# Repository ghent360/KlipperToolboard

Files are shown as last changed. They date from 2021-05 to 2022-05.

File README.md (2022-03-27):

# Huvud 3D Printer toolhead board
This is a modified version of the KilipperBoard started by bondus(https://github.com/bondus/KlipperToolboard). The goal is to make the board as cheap as possible. Removed the CAN interface, switched to RP4020 MCU since it is more available. Added extra IO pins for LEDs or other sensors.
# Original author words
A very small 3D printer board for use on a direct drive toolhead. It is designed to be used with Klipper firmware. Klipper has the awesome feature to be able to use multiple MCUs connected to the host over a (relatively) high latency connection.

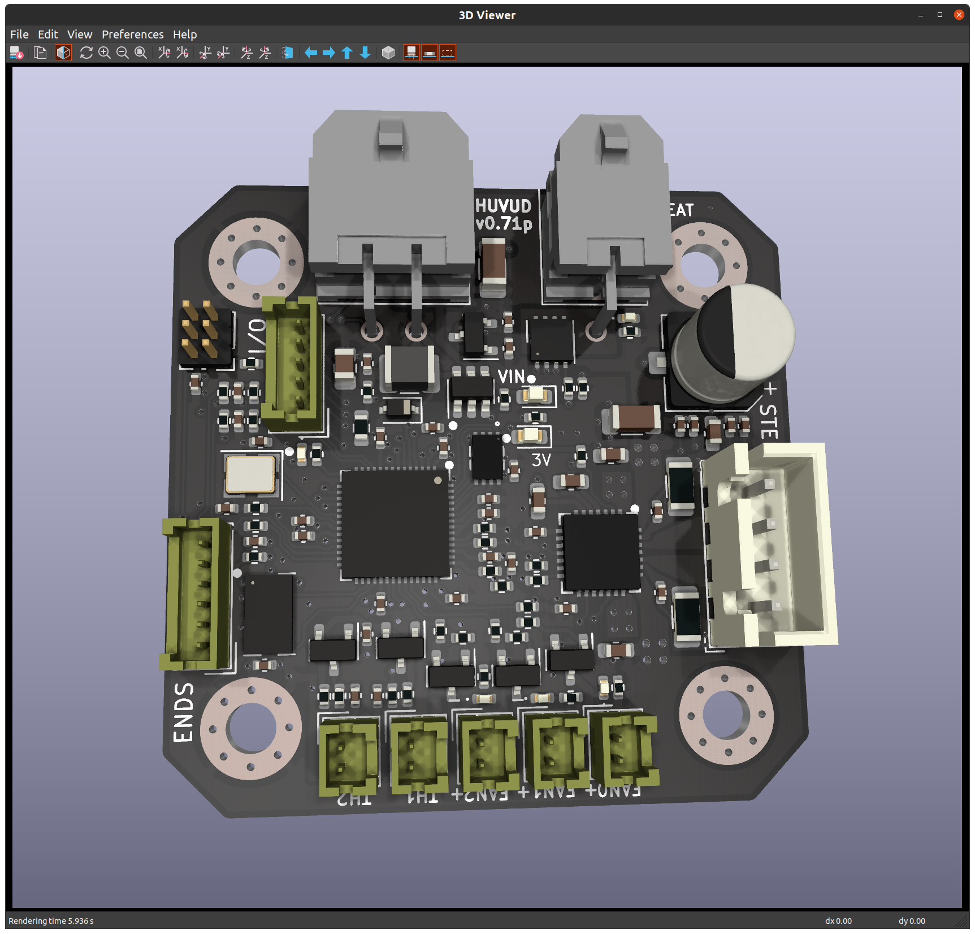
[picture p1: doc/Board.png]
Image of Board


Features: 
* One TMC2209 stepper driver for the extruder
* Three MOSFETs for fans
* One big MOSFET for the hotend heater
* Two thermistor inputs
* ADXL345 accelerometer for resonance testing
* Support for 3 endstops
* 3 extra I/O pins for RGB LEDs or other functions
* RP4020 Dual core 133MHz 32bit ARM MCU
* USB, for flashing firmware

Main power is 12-24V. 24V is preferred to keep the currents low

All done in KiCad and open source. 

If you are interesting in helping out, testing or eventually using this board feel free to contact me at ghent360@iqury.us.

### Documentation

* [Pinout and hook up](doc/pinout.md)
* [Klipper configuration](doc/klipper.md)
* [Prototype versions of the board](doc/versions.md)

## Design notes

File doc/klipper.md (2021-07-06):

## Klipper configuration

### Firmware configuration

* Enable Micro-controller Architecture (STMicroelectronics STM32)
* Pick STM32F103
* Pick Bootloader offset (2KiB bootloader (HID Bootloader))
* Disable Use USB for communication (instead of serial)
* Enable Use CAN for communication (instead of serial)
* Pick CAN pins (Pins PB8(rx) and PB9(tx))

It is possible to use USB instead of the CAN bus, like most other controller boards. 

### Bootloader and Flashing

The boards come preloaded with the HID bootloader for flashing over USB. Note that the board can not be powered over USB. 

To enter the bootloader pin BOOT1 must be connected to 3.3V when the board is powered up or reset. When in the bootloader the green LED will flash quickly. Flash with the command "make flash FLASH_DEVICE=1209:beba"

Hopefully a CAN capable bootloader will be developed to allow flashing over CAN bus.

### printer.cfg

[Example partial printer.cfg](printer.cfg)

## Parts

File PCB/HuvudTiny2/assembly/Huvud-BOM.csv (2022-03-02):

Comment | Designator | Footprint | LCSC | LCSC
0.1uF | C1,C2,C9,C10,C11,C19,C24,C25,C30,C31,C35,C37,C38,C39,C40,C41,C42,C43 | Capacitor_SMD:C_0402_1005Metric |  | C307331
30pF | C12,C13 | Capacitor_SMD:C_0402_1005Metric |  | C1570
10uF/35V | C14,C22 | Capacitor_SMD:C_1206_3216Metric |  | C13585
22uF | C15 | Capacitor_SMD:C_0805_2012Metric |  | C45783
2.2uF | C18,C32,C44 | Capacitor_SMD:C_0402_1005Metric |  | C12530
1nF 50V | C20,C21,C26,C28 | Capacitor_SMD:C_0402_1005Metric |  | C1523
100nF | C29,C36 | Capacitor_SMD:C_0402_1005Metric |  | C1525
0.1uF/35V | C3,C6,C7,C16 | Capacitor_SMD:C_0603_1608Metric |  | C14663
4.7uF | C4,C17,C33,C34 | Capacitor_SMD:C_0402_1005Metric |  | C23733
22nf/50V | C5 | Capacitor_SMD:C_0603_1608Metric |  | C21122
100uF/35V | C8 | Capacitor_SMD:CP_Elec_6.3x7.7 |  | C134792
LEDGR | D1,D2,D3,D5,D10 | LED_SMD:LED_0402_1005Metric |  | C130723
1N5819WS | D4 | Diode_SMD:D_SOD-323 |  | C191023
LEDRED | D6,D8 | LED_SMD:LED_0603_1608Metric |  | C2286
BAT54S | D7,D9 | Package_TO_SOT_SMD:SOT-23 |  | C12765
MountingHole | H1,H2,H3,H4 | MountingHole:MountingHole_3.2mm_M3_Pad_Via
MOLEX Micro Fit 2x2 | J1 | Connector_Molex:Molex_Micro-Fit_3.0_43045-0400_2x02_P3.00mm_Horizontal |  | C122413
FAN0 | J10 | Connector_Hirose:Hirose_DF13-02P-1.25DSA_1x02_P1.25mm_Vertical |  | C10819
IO | J11 | Connector_Hirose:Hirose_DF13-05P-1.25DSA_1x05_P1.25mm_Vertical |  | C220124
DBG | J2 | Connector_PinHeader_1.27mm:PinHeader_2x03_P1.27mm_Vertical
THERM | J3,J8 | Connector_Hirose:Hirose_DF13-02P-1.25DSA_1x02_P1.25mm_Vertical |  | C10819
FAN1 | J4 | Connector_Hirose:Hirose_DF13-02P-1.25DSA_1x02_P1.25mm_Vertical |  | C10819
FAN2 | J5 | Connector_Hirose:Hirose_DF13-02P-1.25DSA_1x02_P1.25mm_Vertical |  | C10819
Heater | J6 | Connector_Molex:Molex_Micro-Fit_3.0_43045-0200_2x01_P3.00mm_Horizontal |  | C122431
Endstop | J7 | Connector_Hirose:Hirose_DF13-06P-1.25DSA_1x06_P1.25mm_Vertical |  | C10823
STEPPER | J9 | Connector_JST:JST_XH_B4B-XH-A_1x04_P2.50mm_Vertical |  | C492489
6.8uH | L1 | Inductor_SMD:L_1210_3225Metric |  | C223222
Logo_Open_Hardware_Small | LOGO1 | Symbol:OSHW-Symbol_6.7x6mm_SilkScreen
Net-Tie_2 | NT1 | NetTie:NetTie-2_SMD_Pad0.5mm
AO3400A | Q1,Q2,Q4 | Package_TO_SOT_SMD:SOT-23 |  | C20917
AON7534 | Q3 | Huvud:DFN-8-1EP_3x3mm_P0.65mm_EP1.7x2.05mm |  | C341712
4.7k | R2,R9 | Resistor_SMD:R_0402_1005Metric |  | C25900
13k | R21 | Resistor_SMD:R_0603_1608Metric |  | C22797
68k | R22 | Resistor_SMD:R_0402_1005Metric |  | C36871
1 | R25 | Resistor_SMD:R_0402_1005Metric |  | C25086
200 | R26 | Resistor_SMD:R_0402_1005Metric |  | C25087
22 | R27,R28,R34,R35 | Resistor_SMD:R_0402_1005Metric |  | C25092
1k | R3,R6,R16,R20,R30 | Resistor_SMD:R_0402_1005Metric |  | C11702
27.4 | R31,R37 | Resistor_SMD:R_0402_1005Metric |  | C31439
0.1 1% | R4,R7 | Resistor_SMD:R_1206_3216Metric |  | C25334
10k | R5,R8,R10,R12,R13,R14,R15,R17,R18,R19,R23,R24,R29,R32,R33,R36,R38,R42,R43 | Resistor_SMD:R_0402_1005Metric |  | C25744
ADXL345 | U1 | Package_LGA:LGA-14_3x5mm_P0.8mm_LayoutBorder1x6y |  | C9667
TMC2209-LA | U2 | Huvud:TMC22xx_QFN |  | C465949
RP2040 | U3 | RP2040_minimal:RP2040-QFN-56 |  | C2040
EUP3458 | U4 | Package_TO_SOT_SMD:SOT-23-6 |  | C89300
XC6206PxxxMR | U5 | Package_TO_SOT_SMD:SOT-23 |  | C5446
W25Q16JVUXIQ | U6 | W25Q16JVUXIQ |  | C2843335
12MHz | Y1 | Crystal:Crystal_SMD_3225-4Pin_3.2x2.5mm |  | C9002

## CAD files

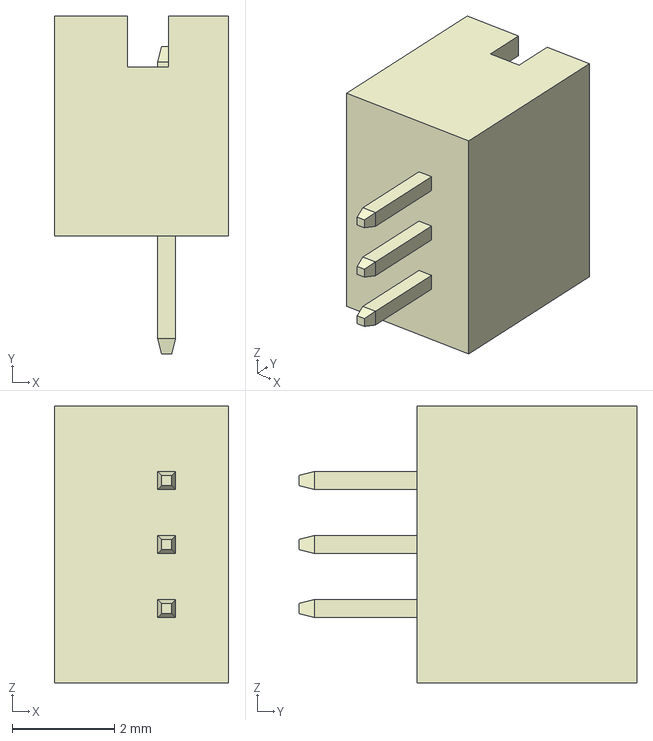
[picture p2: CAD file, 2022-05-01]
PCB/HuvudTiny2/3D/DF13-3P-1.25DSA.stp
3.40 x 6.60 x 5.40 mm

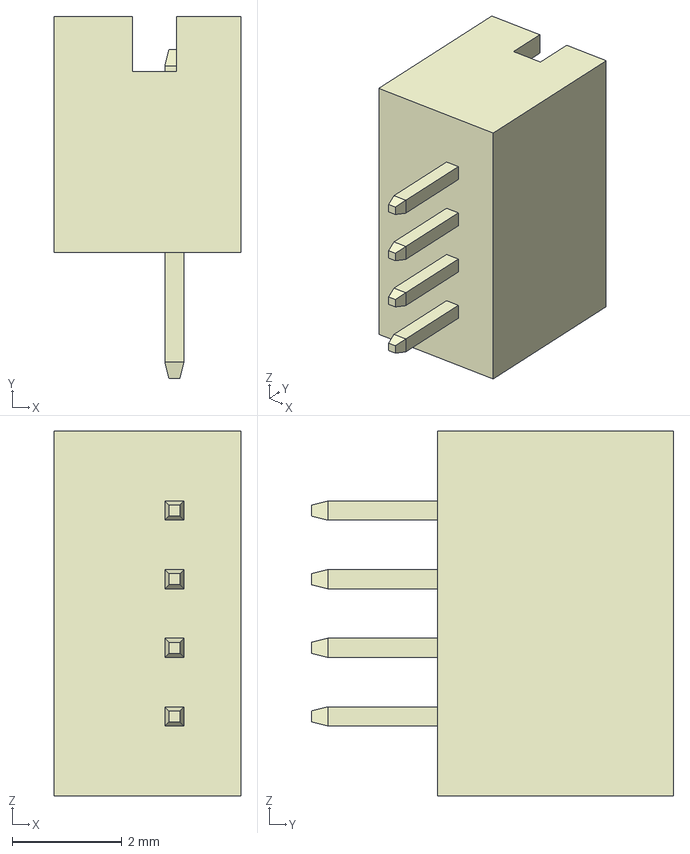
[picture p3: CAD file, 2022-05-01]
PCB/HuvudTiny2/3D/DF13-4P-1.25DSA.stp
3.40 x 6.60 x 6.65 mm

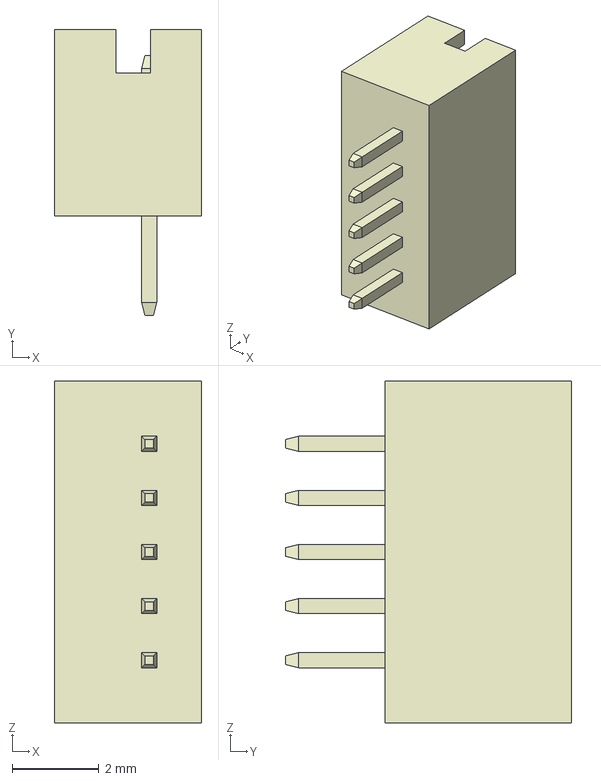
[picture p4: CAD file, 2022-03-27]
PCB/HuvudTiny2/3D/DF13-5P-1.25DSA.stp
3.40 x 6.60 x 7.90 mm

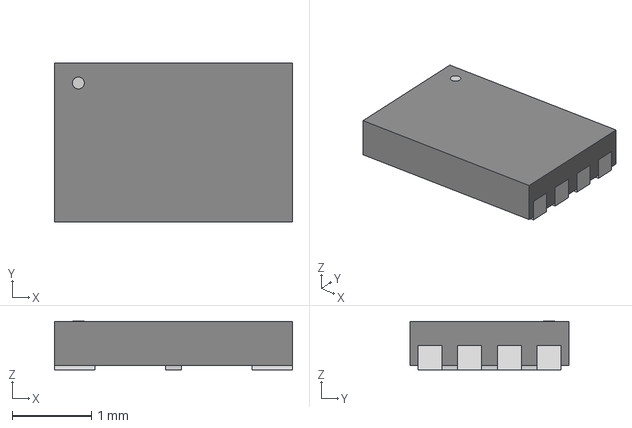
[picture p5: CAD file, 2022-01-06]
PCB/HuvudTiny2/3D/W25Q16JVUXIQ_WIN.step
3.00 x 2.01 x 0.612 mm

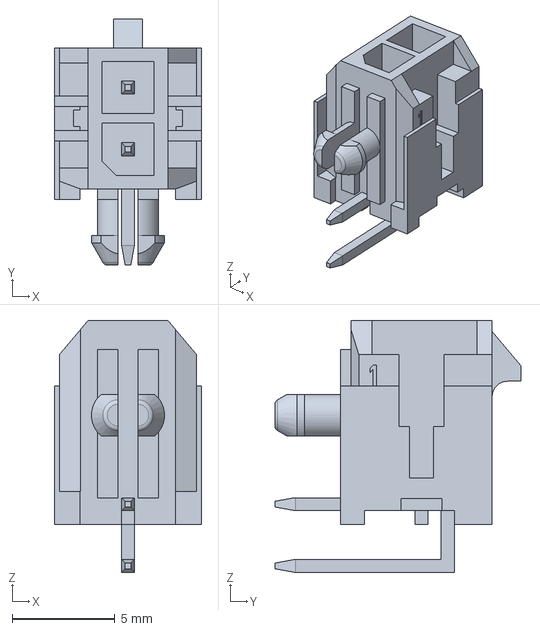
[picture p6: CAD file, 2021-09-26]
PCB/HuvudTiny2/3D/molex_430450200.stp
7.15 x 12.0 x 12.2 mm

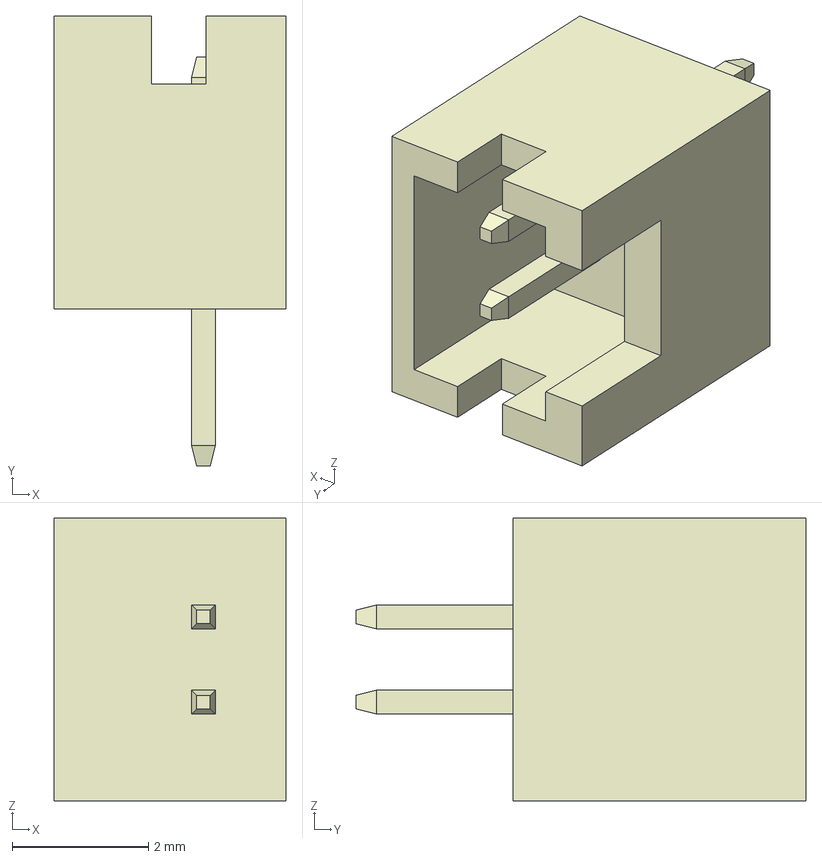
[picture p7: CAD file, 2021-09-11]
PCB/HuvudTiny2/3D/DF13-2P-1.25DSA.stp
3.40 x 6.60 x 4.15 mm

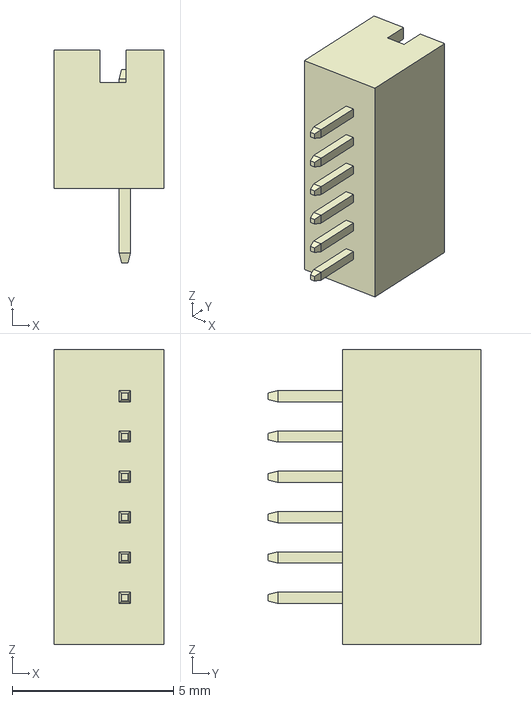
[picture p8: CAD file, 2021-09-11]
PCB/HuvudTiny2/3D/DF13-6P-1.25DSA.stp
3.40 x 6.60 x 9.15 mm

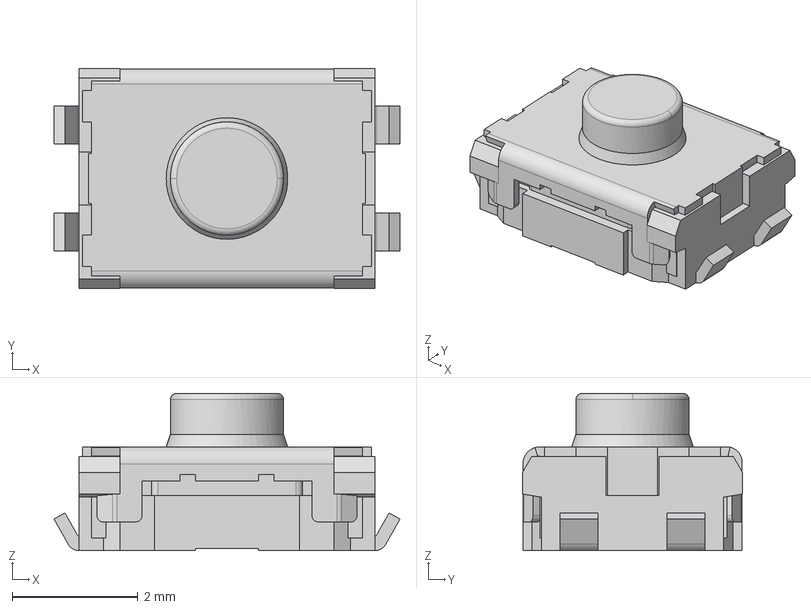
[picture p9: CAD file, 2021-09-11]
PCB/HuvudTiny2/3D/EVQ-P2-H02B_K02Q+3P202K - EVQP2H02B.step
5.50 x 3.50 x 2.50 mm

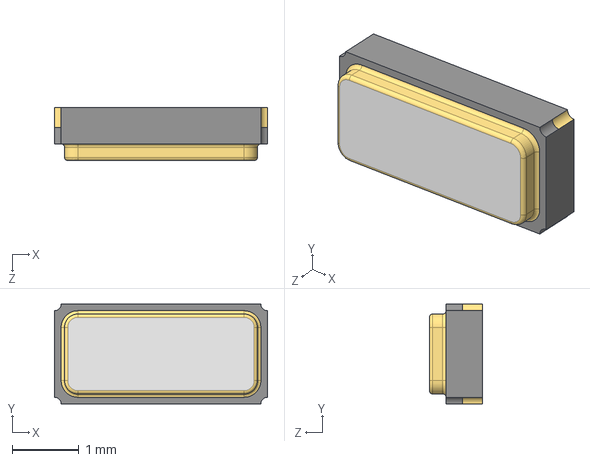
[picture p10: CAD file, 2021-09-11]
PCB/HuvudTiny2/3D/NDK_NX3215SA.step
3.20 x 1.50 x 0.8 mm

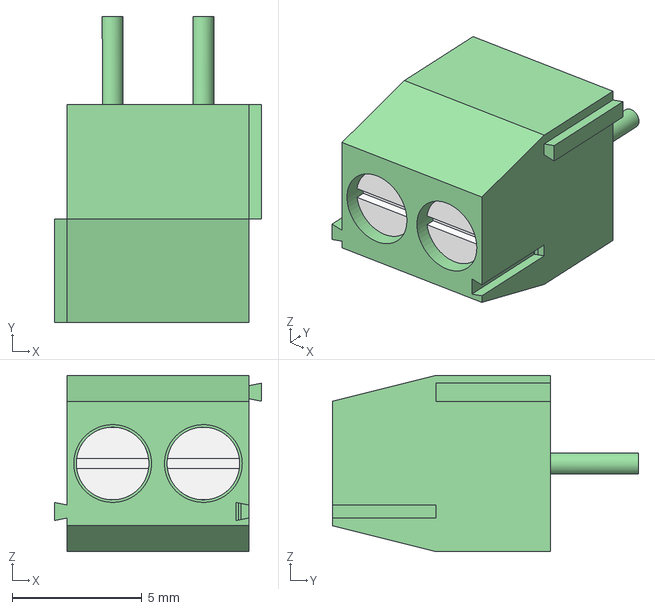
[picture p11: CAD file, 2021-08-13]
PCB/HuvudTiny2/3D/DG350-3,5-02P.step
8.00 x 11.8 x 6.80 mm

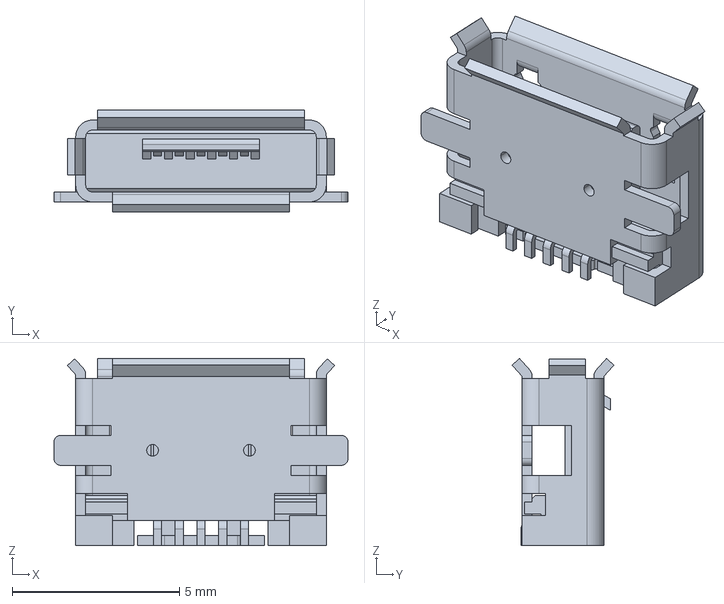
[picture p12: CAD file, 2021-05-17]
PCB/HuvudTiny2/3D/74m6302_1981584-1.step
8.80 x 3.05 x 5.60 mm

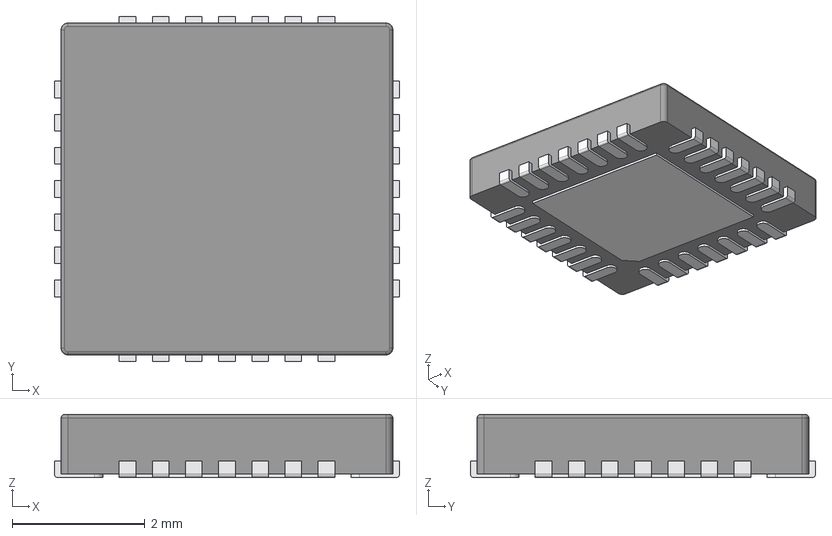
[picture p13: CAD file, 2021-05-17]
PCB/HuvudTiny2/3D/QFN28.step
5.20 x 5.20 x 0.95 mm

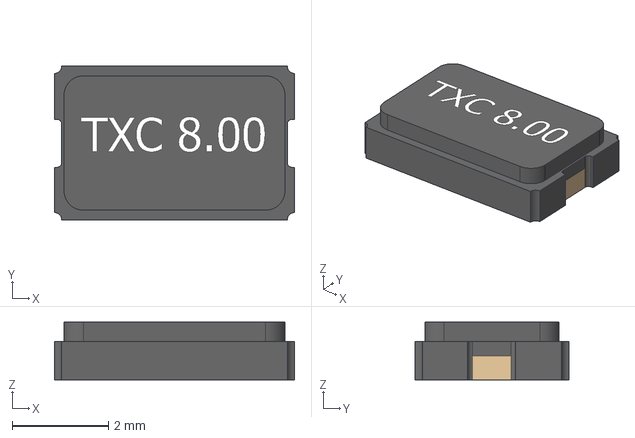
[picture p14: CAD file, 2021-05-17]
PCB/HuvudTiny2/3D/crystal 8MHz.step
5.00 x 3.20 x 1.20 mm

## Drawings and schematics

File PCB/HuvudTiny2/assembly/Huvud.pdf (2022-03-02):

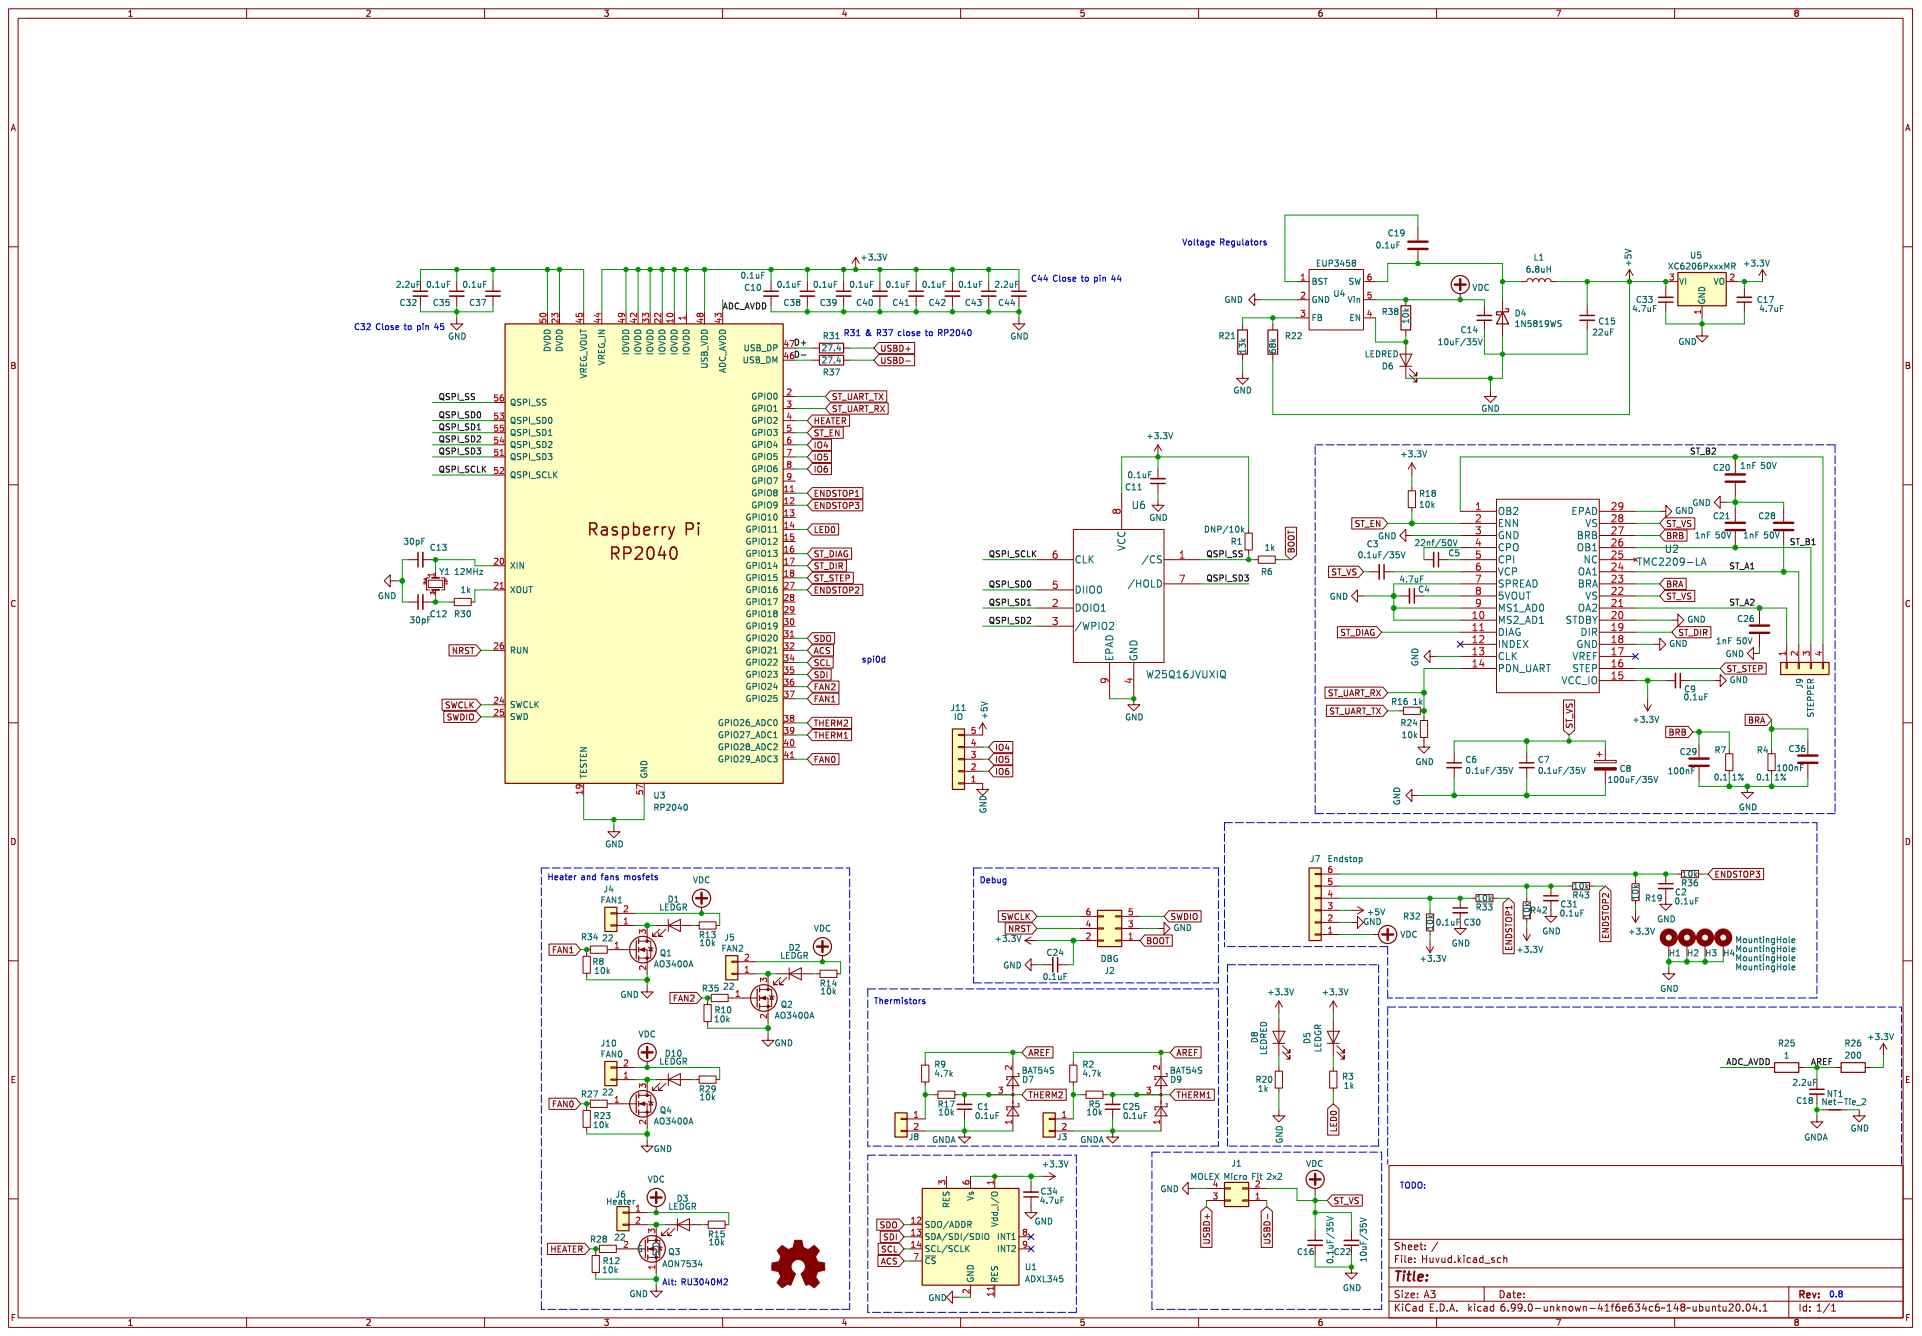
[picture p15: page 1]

1 IOVDD 10 GPIO8 11 GPIO9 12 GPIO10 13 GPIO11 14 GPIO12 15 GPIO13 16 GPIO14 17 GPIO15 18 TESTEN 19 GPIO0 2 XIN 20 XOUT 21 IOVDD 22 DVDD 23 SWCLK 24 SWD 25 RUN 26 GPIO16 27 GPIO17 28 GPIO18 29 GPIO1 3 GPIO19 30 GPIO20 31 GPIO21 32 IOVDD 33 GPIO22 34 GPIO23 35 GPIO24 36 GPIO25 37 GPIO26_ADC0 38 GPIO27_ADC1 39 GPIO2 4 GPIO28_ADC2 40 GPIO29_ADC3 41 IOVDD 42 ADC_AVDD 43 VREG_IN 44 VREG_VOUT 45 USB_DM 46 USB_DP 47 USB_VDD 48 IOVDD 49 GPIO3 5 DVDD 50 QSPI_SD3 51 QSPI_SCLK 52 QSPI_SD0 53 QSPI_SD2 54 QSPI_SD1 55 QSPI_SS 56 GND 57 GPIO4 6 GPIO5 7 GPIO6 8 GPIO7 9 U3RP2040 GND

1 RES 11 SDO/ADDR 12 SDA/SDI/SDIO 13 SCL/SCLK 14 GND

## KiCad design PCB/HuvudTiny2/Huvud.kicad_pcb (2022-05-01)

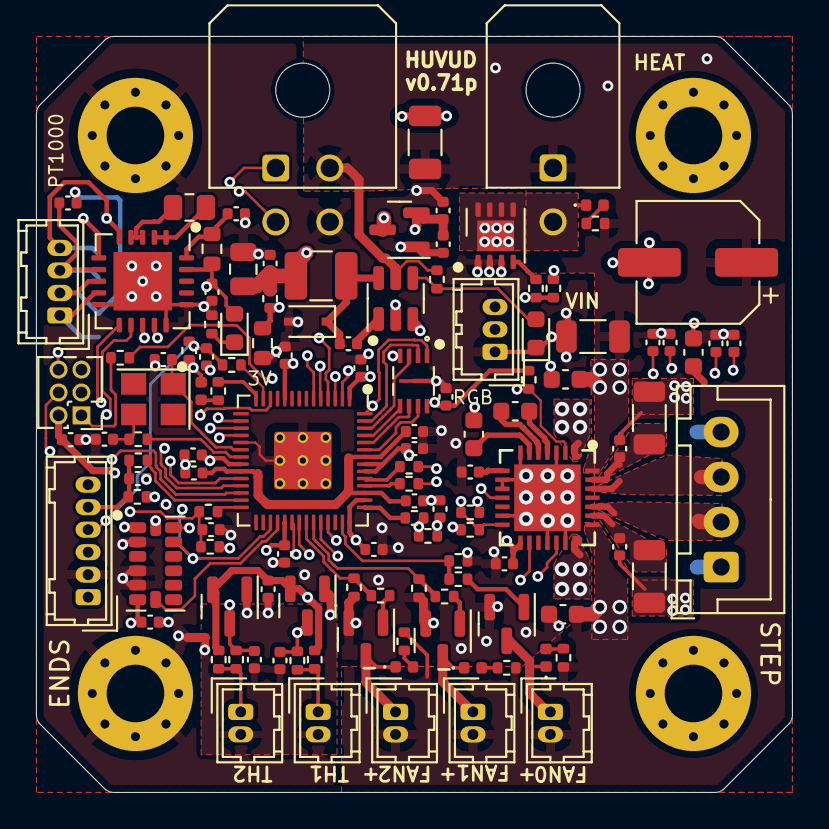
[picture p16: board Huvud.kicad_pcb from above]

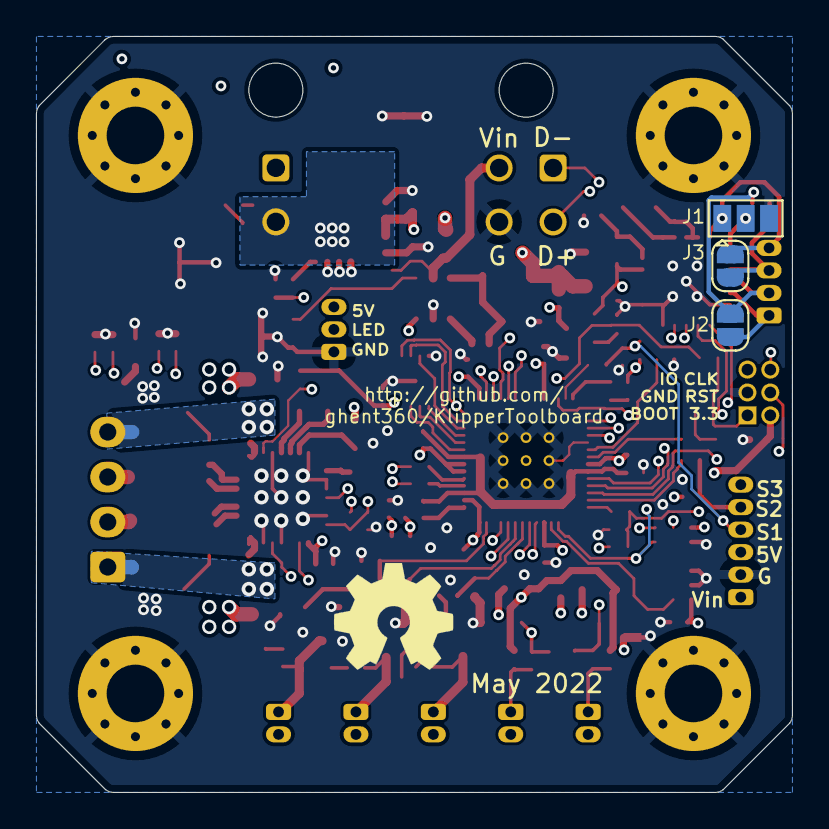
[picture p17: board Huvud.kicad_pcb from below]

Board: 4 copper layers, 42.0 x 42.0 mm, 129 parts (4 on the bottom side), 88 nets.

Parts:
C1, C2, C9, C10, C11, C19, C23, C24, C25, C27, C30, C31, C35, C37, C38, C39, C40, C41, C42, C43, C45: 0.1uF; C_0402_1005Metric
C3, C6, C7, C16: 0.1uF/35V; C_0603_1608Metric
C4, C17, C33, C34: 4.7uF; C_0402_1005Metric
C5: 22nf/50V; C_0603_1608Metric
C8: 100uF/35V; CP_Elec_6.3x7.7
C12, C13: 30pF; C_0402_1005Metric
C14, C22: 10uF/35V; C_1206_3216Metric
C15: 22uF; C_0805_2012Metric
C18, C32, C44: 2.2uF; C_0402_1005Metric
C20, C21, C26, C28: 1nF 50V; C_0402_1005Metric
C29, C36: 100nF; C_0402_1005Metric
D1, D2, D3, D5, D10: LEDGR; LED_0402_1005Metric
D4: 1N5819WS; D_SOD-323
D6, D8: LEDRED; LED_0603_1608Metric
D7, D9: BAT54S; SOT-23
FB1: 600 ohm; R_0603_1608Metric
H1, H2, H3, H4: MountingHole; MountingHole_3.2mm_M3_Pad_Via
J1: MOLEX Micro Fit 2x2; Molex_Micro-Fit_3.0_43045-0400_2x02_P3.00mm_Horizontal
J2: DBG; PinHeader_2x03_P1.27mm_Vertical
J3, J8: THERM; Hirose_DF13-02P-1.25DSA_1x02_P1.25mm_Vertical
J4: FAN1; Hirose_DF13-02P-1.25DSA_1x02_P1.25mm_Vertical
J5: FAN2; Hirose_DF13-02P-1.25DSA_1x02_P1.25mm_Vertical
J6: Heater; Molex_Micro-Fit_3.0_43045-0200_2x01_P3.00mm_Horizontal
J7: Endstop; Hirose_DF13-06P-1.25DSA_1x06_P1.25mm_Vertical
J9: STEPPER; JST_XH_B4B-XH-A_1x04_P2.50mm_Vertical
J10: FAN0; Hirose_DF13-02P-1.25DSA_1x02_P1.25mm_Vertical
J11: IO; Hirose_DF13-03P-1.25DSA_1x03_P1.25mm_Vertical
J12: Conn_01x04; Hirose_DF13-04P-1.25DSA_1x04_P1.25mm_Vertical
JP1: SolderJumper_3_Open; SolderJumper-3_P1.3mm_Open_Pad1.0x1.5mm
JP2, JP3: SolderJumper_2_Open; SolderJumper-2_P1.3mm_Open_RoundedPad1.0x1.5mm
L1: 6.8uH; L_1210_3225Metric
LOGO1: Logo_Open_Hardware_Small; OSHW-Symbol_6.7x6mm_SilkScreen
NT1: Net-Tie_2; NetTie-2_SMD_Pad0.5mm
Q1, Q2, Q4: AO3400A; SOT-23
Q3: AON7534; DFN-8-1EP_3x3mm_P0.65mm_EP1.7x2.05mm
R2, R9: 4.7k; R_0402_1005Metric
R3, R6, R16, R20, R30: 1k; R_0402_1005Metric
R4, R7: 0.1 1%; R_1206_3216Metric
R5, R8, R10, R12, R13, R14, R15, R17, R18, R19, R23, R24, R29, R32, R33, R36, R38, R42, R43: 10k; R_0402_1005Metric
R11: 400; R_0805_2012Metric
R21: 13k; R_0603_1608Metric
R22: 68k; R_0402_1005Metric
R25: 1; R_0402_1005Metric
R26: 200; R_0402_1005Metric
R27, R28, R34, R35: 22; R_0402_1005Metric
R31, R37: 27.4; R_0402_1005Metric
U1: ADXL345; LGA-14_3x5mm_P0.8mm_LayoutBorder1x6y
U2: TMC2209-LA; TMC22xx_QFN
U3: RP2040; RP2040-QFN-56
U4: EUP3458; SOT-23-6
U5: XC6206PxxxMR; SOT-23
U6: W25Q16JVUXIQ
U7: MAX31865xTP; TQFN-20-1EP_5x5mm_P0.65mm_EP3.25x3.25mm
Y1: 12MHz; Crystal_SMD_3225-4Pin_3.2x2.5mm

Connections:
+3V3: C9.2, C10.1, C11.2, C17.2, C23.2, C24.1, C34.2, C38.1, C39.1, C40.1, C41.1, C42.1, C43.1, C44.1, D5.2 (A), D8.2 (A), FB1.1, J2.2, R18.1, R19.1, R26.2, R32.1, R42.1, U1.1 (Vdd_I/O), U1.6 (Vs), U2.15 (VCC_IO), U3.1 (IOVDD), U3.10 (IOVDD), U3.22 (IOVDD), U3.33 (IOVDD), U3.42 (IOVDD), U3.44 (VREG_IN), U3.48 (USB_VDD), U3.49 (IOVDD), U5.2 (VO), U6.8 (VCC), U7.19 (DVDD)
+5V: C15.1, C33.2, J7.3, J11.3, L1.2, R22.2, U5.3 (VI)
/ADC_AVDD: R25.1, U3.43 (ADC_AVDD)
/D+: R31.1, U3.47 (USB_DP)
/D-: R37.1, U3.46 (USB_DM)
/QSPI_SCLK: U3.52 (QSPI_SCLK), U6.6 (CLK)
/QSPI_SD0: U3.53 (QSPI_SD0), U6.5 (DIIO0)
/QSPI_SD1: U3.55 (QSPI_SD1), U6.2 (DOIO1)
/QSPI_SD2: U3.54 (QSPI_SD2), U6.3 (/WPIO2)
/QSPI_SD3: U3.51 (QSPI_SD3), U6.7 (/HOLD)
/QSPI_SS: R6.1, U3.56 (QSPI_SS), U6.1 (/CS)
/ST_A1: C28.2, J9.2, U2.24 (OA1)
/ST_A2: C26.1, J9.1, U2.21 (OA2)
/ST_B1: C21.2, J9.3, U2.26 (OB1)
/ST_B2: C20.1, J9.4, U2.1 (OB2)
ACS: U1.7 (~CS), U3.32 (GPIO21)
AREF: C18.1, D7.2, D9.2, R2.2, R9.2, R25.2, R26.1
BOOT: J2.1, R6.2
BRA: C36.1, R4.2, U2.23 (BRA)
BRB: C29.1, R7.2, U2.27 (BRB)
ENDSTOP1: R33.2, U3.13 (GPIO10)
ENDSTOP2: R43.2, U3.27 (GPIO16)
ENDSTOP3: R36.2, U3.28 (GPIO17)
FAN0: R23.1, R27.1, U3.41 (GPIO29_ADC3)
FAN1: R8.2, R34.1, U3.37 (GPIO25)
FAN2: R10.1, R35.1, U3.36 (GPIO24)
GND: C2.2, C4.2, C6.2, C7.2, C8.2, C9.1, C10.2, C11.1, C12.1, C13.1, C14.1, C15.2, C16.2, C17.1, C20.2, C21.1, C22.1, C23.1, C24.2, C26.2, C27.1, C28.1, C29.2, C30.2, C31.2, C32.2, C33.1, C34.1, C35.2, C36.2, C37.2, C38.2, C39.2, C40.2, C41.2, C42.2, C43.2, C44.2, D4.2 (A), D6.1 (K), H1.1, H2.1, H3.1, H4.1, J1.4, J2.3, J7.2, J11.1, JP1.3 (B), NT1.1, Q1.2 (S), Q2.2 (S), Q3.1 (S), Q4.2 (S), R4.1, R7.1, R8.1, R10.2, R12.2, R20.2, R21.2, R23.2, R24.1, U1.2 (GND), U1.4 (GND), U1.5 (GND), U2.3 (GND), U2.7 (SPREAD), U2.9 (MS1_AD0), U2.10 (MS2_AD1), U2.13 (CLK), U2.18 (GND), U2.20 (STDBY), U2.29 (EPAD), U3.19 (TESTEN), U3.57 (GND), U4.2 (GND), U5.1 (GND), U6.4 (GND), U6.9 (EPAD), U7.10 (GND), U7.15 (DGND), U7.16 (GND), U7.21 (GND)
GNDA: C1.1, C18.2, C25.1, D7.1, D9.1, J3.2, J8.2, NT1.2
HEATER: R12.1, R28.1, U3.4 (GPIO2)
IO4: J11.2, U3.6 (GPIO4)
LED0: R3.1, U3.14 (GPIO11)
MCS: U3.12 (GPIO9), U7.13 (~CS)
NRST: J2.4, U3.26 (RUN)
unnamed: C12.2, R30.1, Y1.3
unnamed: D1.2 (A), R13.2
unnamed: D1.1 (K), J4.1, Q1.3 (D)
unnamed: D2.2 (A), R14.2
unnamed: D2.1 (K), J5.1, Q2.3 (D)
unnamed: D3.2 (A), R15.2
unnamed: D3.1 (K), J6.2, Q3.3 (D)
unnamed: C19.2, D4.1 (K), L1.1, U4.6 (SW)
unnamed: D5.1 (K), R3.2
unnamed: D6.2 (A), R38.2, U4.4 (EN)
unnamed: D8.1 (K), R20.1
unnamed: D10.2 (A), R29.2
unnamed: D10.1 (K), J10.1, Q4.3 (D)
unnamed: J3.1, R2.1, R5.2
unnamed: C30.1, J7.4, R32.2, R33.1
unnamed: C31.1, J7.5, R42.2, R43.1
unnamed: C2.1, J7.6, R19.2, R36.1
unnamed: J8.1, R9.1, R17.2
unnamed: J12.1, JP3.1 (A), U7.9 (FORCE-)
unnamed: C45.1, J12.2, JP3.2 (B), U7.8 (RTDIN-)
unnamed: C45.2, J12.3, JP2.1 (A), U7.7 (RTDIN+)
unnamed: J12.4, JP1.1 (A), JP2.2 (B), U7.5 (FORCE+)
unnamed: JP1.2 (C), U7.6 (FORCE2)
unnamed: Q1.1 (G), R34.2
unnamed: Q2.1 (G), R35.2
unnamed: Q3.2 (G), R28.2
unnamed: Q4.1 (G), R27.2
unnamed: C4.1, U2.8 (5VOUT)
unnamed: C5.1, U2.5 (CPI)
unnamed: C5.2, U2.4 (CPO)
unnamed: C3.1, U2.6 (VCP)
unnamed: C32.1, C35.1, C37.1, U3.23 (DVDD), U3.45 (VREG_VOUT), U3.50 (DVDD)
unnamed: C13.2, U3.20 (XIN), Y1.1
unnamed: R30.2, U3.21 (XOUT)
unnamed: C19.1, U4.1 (BST)
unnamed: R21.1, R22.1, U4.3 (FB)
unnamed: R11.1, U7.1 (BIAS), U7.2 (REFIN+)
unnamed: R11.2, U7.3 (REFIN-), U7.4 (ISENSOR)
unnamed: C27.2, FB1.2, U7.20 (VDD)
SCL: U1.14 (SCL/SCLK), U3.34 (GPIO22), U7.12 (SCLK)
SDI: U1.13 (SDA/SDI/SDIO), U3.35 (GPIO23), U7.11 (SDI)
SDO: U1.12 (SDO/ADDR), U3.31 (GPIO20), U7.14 (SDO)
ST_DIAG: U2.11 (DIAG), U3.16 (GPIO13)
ST_DIR: U2.19 (DIR), U3.17 (GPIO14)
ST_EN: R18.2, U2.2 (ENN), U3.5 (GPIO3)
ST_STEP: U2.16 (STEP), U3.18 (GPIO15)
ST_UART_RX: R16.2, R24.2, U2.14 (PDN_UART), U3.3 (GPIO1)
ST_UART_TX: R16.1, U3.2 (GPIO0)
ST_VS: C3.2, C6.1, C7.1, C8.1, C14.2, C16.1, C22.2, J1.2, J4.2, J5.2, J6.1, J7.1, J10.2, R13.1, R14.1, R15.1, R29.1, R38.1, U2.22 (VS), U2.28 (VS), U4.5 (Vin)
SWCLK: J2.6, U3.24 (SWCLK)
SWDIO: J2.5, U3.25 (SWD)
THERM1: C25.2, D9.3, R5.1, U3.39 (GPIO27_ADC1)
THERM2: C1.2, D7.3, R17.1, U3.38 (GPIO26_ADC0)
USBD+: J1.3, R31.2
USBD-: J1.1, R37.2

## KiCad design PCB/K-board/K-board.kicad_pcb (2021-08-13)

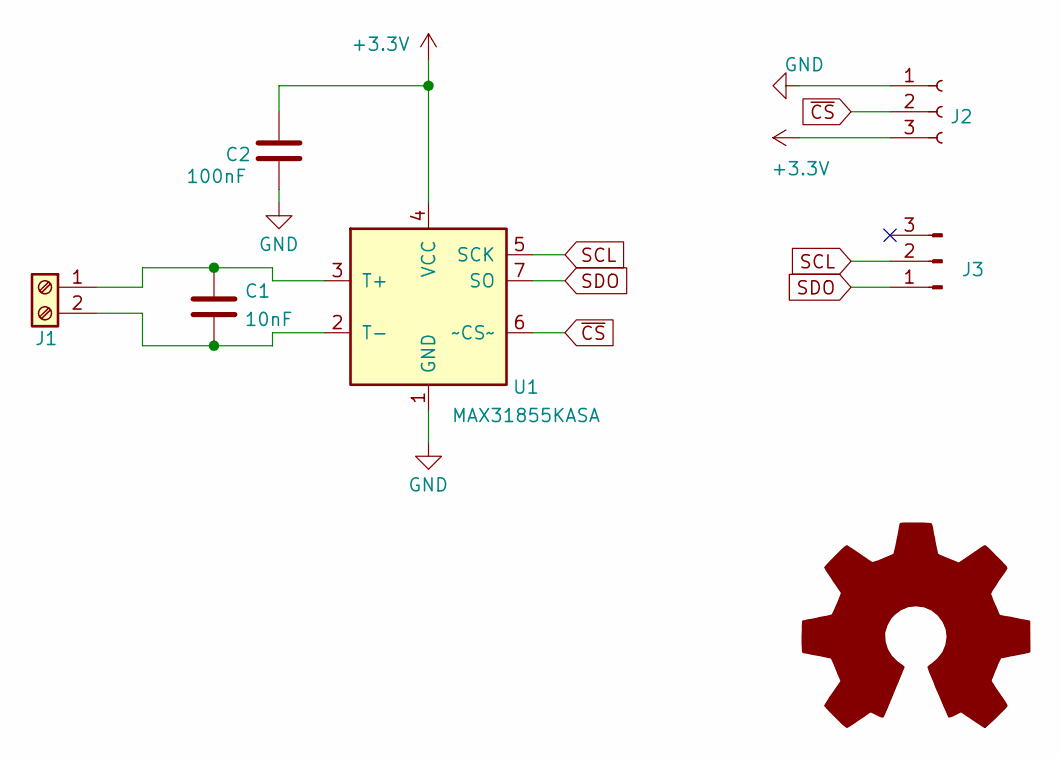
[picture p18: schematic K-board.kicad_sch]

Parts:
C1: 10nF; C_0402_1005Metric; LCSC C15195
C2: 100nF; C_0402_1005Metric; LCSC C1525
J1: Screw_Terminal_01x02; TerminalBlock_Phoenix_PT-1,5-2-3.5-H_1x02_P3.50mm_Horizontal
J2: Conn_01x03_Female; PinSocket_1x03_P1.27mm_Vertical
J3: Conn_01x03_Male; PinHeader_1x03_P1.27mm_Vertical
U1: MAX31855KASA; SOIC-8_3.9x4.9mm_P1.27mm; LCSC C52028

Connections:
+3V3: C2.1, J2.3, U1.4 (VCC)
GND: C2.2, J2.1, U1.1 (GND)
unnamed: C1.1, J1.1, U1.3 (T+)
unnamed: C1.2, J1.2, U1.2 (T-)
SCL: J3.2, U1.5 (SCK)
SDO: J3.1, U1.7 (SO)
~CS: J2.2, U1.6 (~CS~)

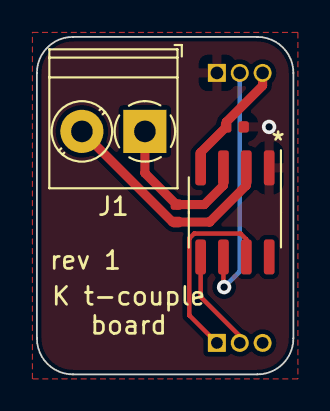
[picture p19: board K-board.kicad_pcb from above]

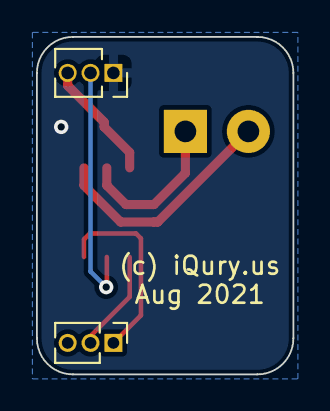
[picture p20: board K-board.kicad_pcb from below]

Board: 2 copper layers, 14.2 x 18.8 mm, 6 parts (2 on the bottom side), 7 nets.

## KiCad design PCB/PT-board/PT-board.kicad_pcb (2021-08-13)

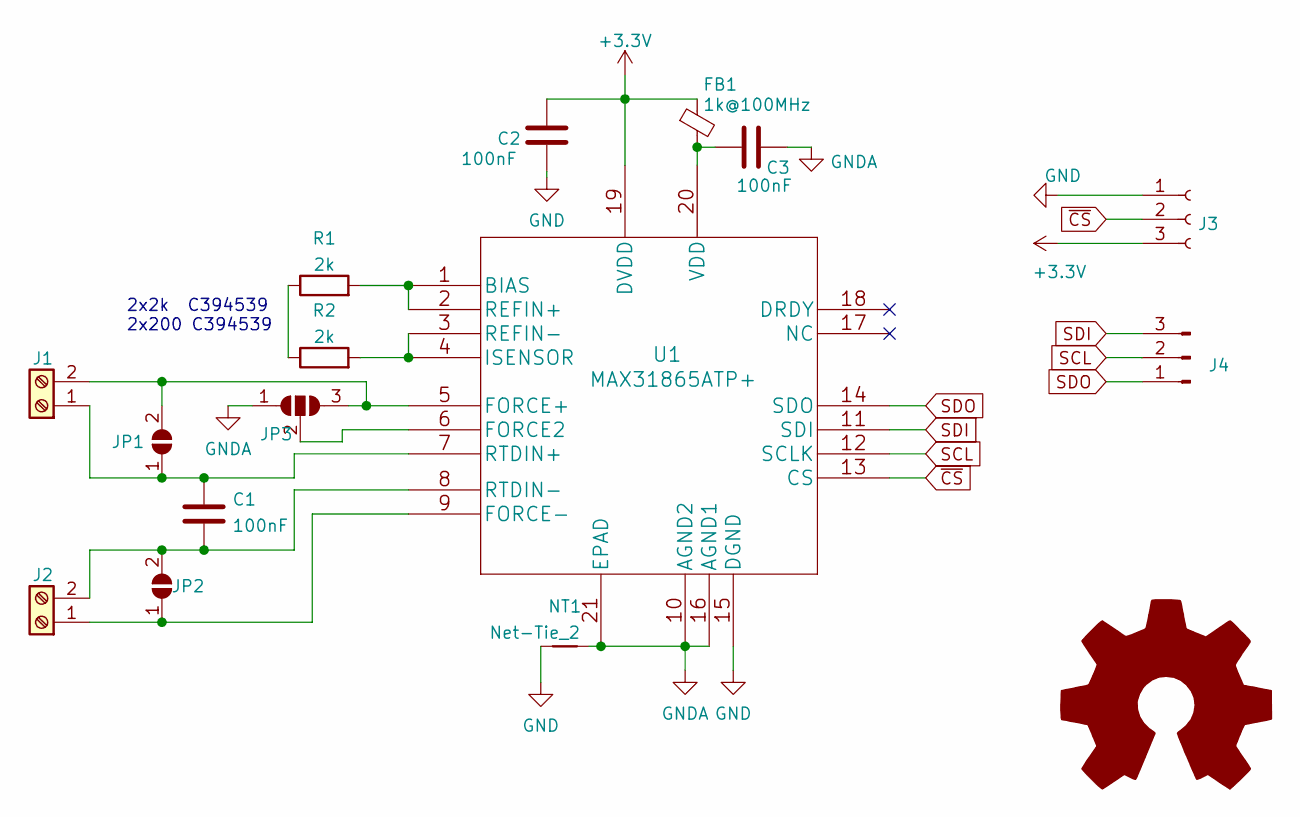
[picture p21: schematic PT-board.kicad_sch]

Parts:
C1, C2, C3: 100nF; C_0402_1005Metric; LCSC C1525
FB1: 1k@100MHz; L_0402_1005Metric; LCSC C85819
J1, J2: Screw_Terminal_01x02; TerminalBlock_Phoenix_PT-1,5-2-3.5-H_1x02_P3.50mm_Horizontal
J3: Conn_01x03_Female; PinSocket_1x03_P1.27mm_Vertical
J4: Conn_01x03_Male; PinHeader_1x03_P1.27mm_Vertical
JP1, JP2: SolderJumper_2_Open; SolderJumper-2_P1.3mm_Open_TrianglePad1.0x1.5mm
JP3: SolderJumper_3_Open; SolderJumper-3_P1.3mm_Open_RoundedPad1.0x1.5mm_NumberLabels
NT1: Net-Tie_2; NetTie-2_SMD_Pad0.5mm
R1, R2: 2k; R_0603_1608Metric; LCSC C394539
U1: MAX31865ATP+; MAX31865ATP

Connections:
+3V3: C2.1, FB1.1, J3.3, U1.19 (DVDD)
GND: C2.2, J3.1, NT1.1, U1.15 (DGND)
GNDA: C3.2, JP3.1 (A), NT1.2, U1.10 (AGND2), U1.16 (AGND1), U1.21 (EPAD)
unnamed: C1.1, J1.1, JP1.1 (A), U1.7 (RTDIN+)
unnamed: C1.2, J2.2, JP2.2 (B), U1.8 (RTDIN-)
unnamed: C3.1, FB1.2, U1.20 (VDD)
unnamed: J1.2, JP1.2 (B), JP3.3 (B), U1.5 (FORCE+)
unnamed: J2.1, JP2.1 (A), U1.9 (FORCE-)
unnamed: JP3.2 (C), U1.6 (FORCE2)
unnamed: R1.1, R2.1
unnamed: R1.2, U1.1 (BIAS), U1.2 (REFIN+)
unnamed: R2.2, U1.3 (REFIN-), U1.4 (ISENSOR)
SCL: J4.2, U1.12 (SCLK)
SDI: J4.3, U1.11 (SDI)
SDO: J4.1, U1.14 (SDO)
~CS: J3.2, U1.13 (CS)

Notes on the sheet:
2x2k C394539 2x200 C394539

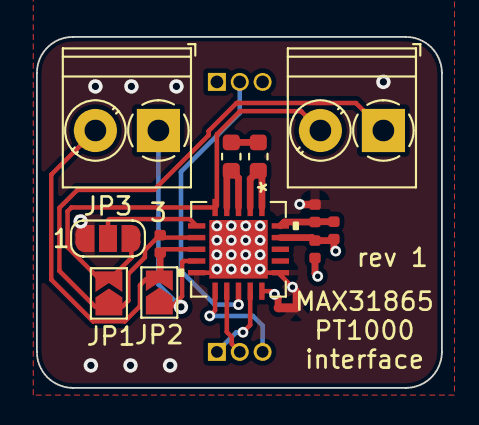
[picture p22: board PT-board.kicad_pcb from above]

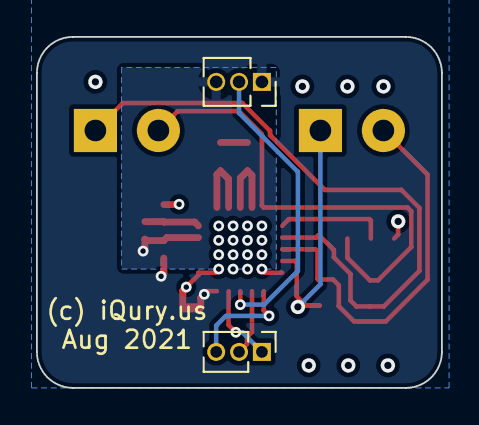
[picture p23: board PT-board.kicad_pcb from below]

Board: 4 copper layers, 22.5 x 19.5 mm, 15 parts (2 on the bottom side), 16 nets.

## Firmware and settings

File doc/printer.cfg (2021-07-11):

# A partial printer.cfg for using the huvud control board
#
#

[mcu head0]
serial: /dev/serial/by-id/usb-Klipper_stm32f103xe_51FF6E067266545230331767-if00 # Change to your ID
restart_method: command

[static_digital_output my_output_pins]
pins: head0:PB6 # Power up the stepper driver

[extruder]
step_pin: head0:PB3
dir_pin: head0:PB4
enable_pin: !head0:PB5
heater_pin: head0:PA6  # "HEAT"
step_distance: .002
nozzle_diameter: 0.400
filament_diameter: 1.750
sensor_type: EPCOS 100K B57560G104F
sensor_pin: head0:PA0 # "THERMISTOR"
pullup_resistor: 4700 # The board uses a 4.7k ohm pullup to work with a PT1000 
min_temp: 0
max_temp: 250

[tmc2209 extruder]
uart_pin: head0:PA10
tx_pin: head0:PA9
microsteps: 16
interpolate: True
run_current: 0.7
sense_resistor: 0.1
hold_current: 0.5
stealthchop_threshold: 0


[heater_fan extruder_fan]
pin: head0:PA8   # "FAN1"
heater: extruder
heater_temp: 50.0

[fan]
pin: head0:PA7  # "FAN0"


# endstop_pin = head0:PB10  "ENDSTOP", active low
# endstop_pin = head0:PB11  "ENDSTOP", active low
# endstop_pin = head0:PB12  "ENDSTOP", active low

[adxl345]
cs_pin: head0:PB1
spi_speed: 5000000
spi_bus: spi2
axes_map: x,y,z
#   The accelerometer axis for each of the printer's x, y, and z axes.
#   This may be useful if the accelerometer is mounted in an
#   orientation that does not match the printer orientation. For
#   example, one could set this to "y,x,z" to swap the x and y axes.
#   It is also possible to negate an axis if the accelerometer
#   direction is reversed (eg, "x,z,-y"). The default is "x,y,z".
rate: 3200

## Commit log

2021-05-17 Convert to Kicad 6.
    [Huvud.kicad_pcb, Huvud.kicad_sch]
2021-05-17 Power from USB, remove CAN. Update micro USB footprint. Update TMC footprint.
    [74m6302_1981584-1.step, Huvud.kicad_pcb, Huvud.kicad_sch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]
2021-05-22 Improve power routing. Fix TH input protection.
    [Huvud.kicad_pcb, Huvud.kicad_sch]
2021-05-22 Generated gerber files.
    [Huvud.kicad_pcb, Huvud.kicad_sch]
2021-05-24 Add all R1 files - sent to fab.
    [Huvud-BOM.csv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]
2021-05-24 Make C8 label invisible on PCB.
    [Huvud.kicad_pcb]
2021-05-24 Removed old board variants. Updated the readme.
    [B4B-ZR-3.4.STEP, B4B-ZR-SM4-TF.STEP, B4B-ZR.STEP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]
2021-05-24 Add protection diode on endstop 1. Add back heatsink for power mosfet.
    [Huvud.kicad_pcb, Huvud.kicad_sch]
2021-05-25 Update sense resistors to 0.1 1206 size.
    [Huvud.kicad_pcb, Huvud.kicad_sch]
2021-05-25 Route VCC_IO to GPIO pin so we can reset the stepper driver.
    [Huvud.kicad_pcb, Huvud.kicad_sch]
2021-07-05 Added caps across stepper pins.
    [Huvud.kicad_pcb, Huvud.kicad_sch]
2021-07-05 Add caps across current sense resistors.
    [Huvud.kicad_pcb, Huvud.kicad_sch]
2021-07-05 Small tweaks to footprints.
    [Huvud.kicad_pcb, Huvud.kicad_sch]
2021-07-11 Update config for 0.6
    [printer.cfg]
2021-07-12 Replaced MCU with SAMD21
    [Huvud.kicad_sch]
2021-07-12 Some routing.
    [Huvud.kicad_pcb, Huvud.kicad_sch]
2021-07-12 Routing complete.
    [Huvud.kicad_pcb]
2021-07-12 Routed with 32k crystal.
    [Huvud.kicad_pcb, Huvud.kicad_sch]
2021-07-26 Update PCB routing.
    [Huvud.kicad_pcb]
2021-07-31 Genedare manufacturing files. Send to fab. Make sligh routing mods after the fab output.
    [Huvud-BOM.csv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]
2021-08-01 Layout improvements.
    [Huvud.kicad_pcb]
2021-08-11 Flipped FAN connectors. Changed pinout on endstop connector. Added SPI thermocouple connector - shared CS with THERMISTOR.
    [Huvud.kicad_pcb, Huvud.kicad_sch]
2021-08-11 Round PCB corners.
    [Huvud.kicad_pcb]
2021-08-13 Add PT1000 board.
    [PT-board.kicad_pcb, PT-board.kicad_sch]
2021-08-13 Update PT board size and move filter cap on the Huvud so ethe two boards can actually be attached together.
    [Huvud.kicad_pcb, PT-board.kicad_pcb]
2021-08-13 Added K-type thermocouple board based on MAX31855.
    [K-board.kicad_pcb, K-board.kicad_sch, PT-board.kicad_sch]
2021-08-23 Improve sense resistor ground. Improve power mosfer routing. Set PCB color and copper finish.
    [Huvud.kicad_pcb]
2021-09-11 Route new version with 1.25mm connectors. Added TH2 and 24V on the endstop connector.
    [DF13-2P-1.25DSA.stp, DF13-6P-1.25DSA.stp, EVQ-P2-H02B_K02Q+3P202K - EVQP2H02B.step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]
2021-09-17 Switched power & USB to MOLEX MicroFit 2x6. Switched heater to 3.5mm terminal.
    [430450600.stp, DG350-3,5-02P.step, Huvud.kicad_pcb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]
2021-09-17 Updated GNDA layout.
    [Huvud.kicad_pcb]
2021-09-24 Update screw terminal to molex connector.
    [Huvud.kicad_pcb, Huvud.kicad_sch]
2021-09-26 Finished routing.
    [430450200.stp, Huvud.kicad_pcb]
2021-09-26 Clean PCB routing.
    [Huvud.kicad_pcb]
2021-09-26 Remove all traces this time for real.
    [Huvud.kicad_pcb]
2021-09-26 Stepper power routed.
    [Huvud.kicad_pcb]
2021-09-26 Routed all traces.
    [Huvud.kicad_pcb]
2021-09-26 Improve layout.
    [Huvud.kicad_pcb]
2021-10-01 Add third fan mosfet (could be used for lighing).
    [Huvud.kicad_pcb, Huvud.kicad_sch]
2021-10-09 LDO power supply from 24V.
    [Huvud.kicad_pcb, Huvud.kicad_sch]
2021-10-10 Re work power supply added 5V stage: 24v->5V->3.3V
    [430450600.stp, Huvud.kicad_pcb, Huvud.kicad_sch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]
2021-10-10 Resolve DRC warnings.
    [Huvud.kicad_pcb]
2021-10-10 Add LCSC component for the MCU.
    [Huvud.kicad_sch]
2021-10-10 Update fabrication files.
    [Huvud-BOM.csv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]
2021-10-10 Update PCB to match with schematics metadata. Re generate interactive BOM.
    [Huvud.kicad_pcb]
2022-01-06 Added footprint libraries.
2022-01-06 Remove SAMD21 part update chrystal to 12MHz.
    [Huvud.kicad_sch]
2022-01-06 Add SPI flash symbol.
    [Huvud.kicad_pcb, Huvud.kicad_sch, W25Q16JVUXIQ_WIN.step]
2022-01-06 Added RP2040 and hooked power, USB and analog in the schematics.
    [Huvud.kicad_sch]
2022-01-06 Almost all components are on the board.
    [Huvud.kicad_pcb, Huvud.kicad_sch]
2022-01-07 Fully routed. Some 3D models are messed up.
    [Huvud.kicad_pcb, Huvud.kicad_sch]
2022-03-02 Add new buck cvtr as power supply. Re-route the board.
    [Huvud-BOM.csv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]
2022-03-27 Updated silk screen. Added soem extra GND vias. Updated 3D models.
    [DF13-5P-1.25DSA.stp, Huvud.kicad_pcb]
2022-03-30 Improve GND connection on some components.
    [Huvud.kicad_pcb]
2022-04-18 Add PT100 reader.
    [Huvud.kicad_pcb, Huvud.kicad_sch]
2022-04-18 re-layout the board to accomodate the PT100 reader chip.
    [Huvud.kicad_pcb, Huvud.kicad_sch]
2022-04-24 Updated some traces, fixed minor DRC issues.
    [Huvud.kicad_pcb]
2022-04-24 Placed all components. Routed some more traces.
    [Huvud.kicad_pcb, Huvud.kicad_sch]
2022-05-01 Update 3d model paths.
    [Huvud.kicad_pcb]
2022-05-01 Fix all 3d models. DRC passes.
    [DF13-3P-1.25DSA.stp, DF13-4P-1.25DSA.stp, Huvud.kicad_pcb]

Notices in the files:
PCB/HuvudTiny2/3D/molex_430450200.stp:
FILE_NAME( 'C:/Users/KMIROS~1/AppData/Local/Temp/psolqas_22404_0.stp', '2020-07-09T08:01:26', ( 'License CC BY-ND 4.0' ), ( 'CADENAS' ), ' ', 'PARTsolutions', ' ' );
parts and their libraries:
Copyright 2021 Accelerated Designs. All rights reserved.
